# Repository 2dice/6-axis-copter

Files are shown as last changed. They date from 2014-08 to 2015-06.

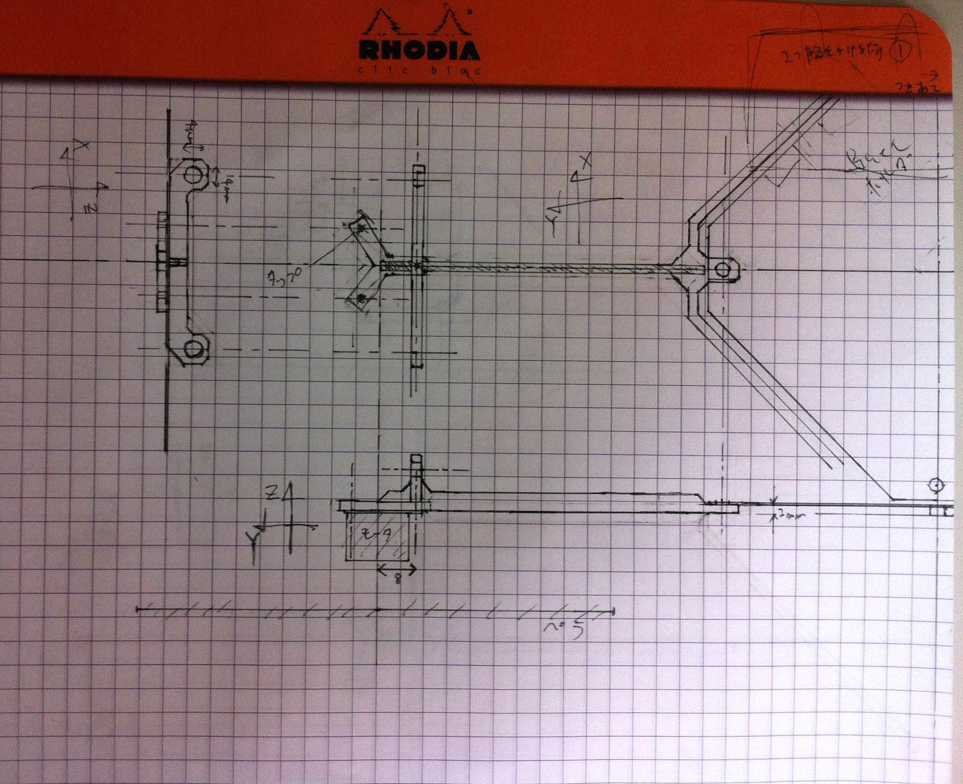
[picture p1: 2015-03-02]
devlog/picture/2015.03.01_2xframe_draft-1.JPG

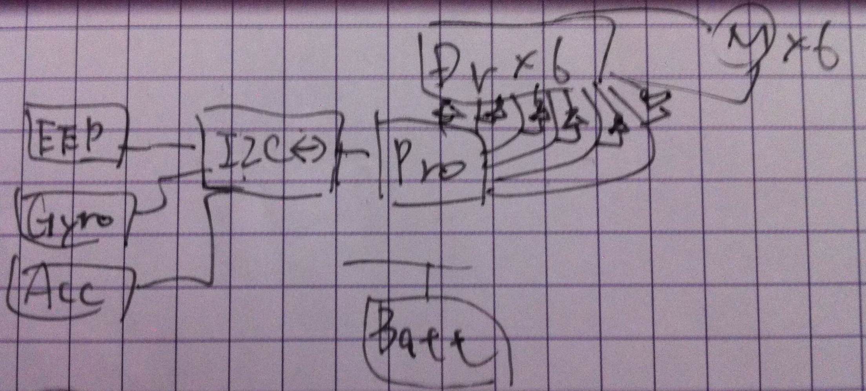
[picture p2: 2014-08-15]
devlog/picture/2014.08.09_circuit-block-image.JPG

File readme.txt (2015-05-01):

■6軸コプター概要
6軸に移動可能なマルチコプターを6個のプロペラで実現することを目標としている．
最終的には自動で衝突回避・PCからコマンドを受信しアクロバットな動きをさせる．

■開発フェーズ
ラフ設計段階
・電子回路
	1x基板(コアレス->ブラシモータ)浮力不足により2xでブラシレスモータ試作
	2x基板作成中
・アクチュエータ
	ブラシレスモータ・プロペラ仮選定済み．2xで浮力確認
・ソフトウェア
	デバイスドライバ仮実装完了．
	2x基板作成後最終確認．その後モータ制御実装．
・筐体
	2x向け設計完了(3Dプリント中)

■ディレクトリ構成
./datasheet
	電子回路に使用している部品のデータシート置き場
./devlog
	開発記録
./schematic
	**.sch
		回路図(kicad)
	**.kicad_pcb
		基板図(kicad)
	librarys
		回路図に使用したライブラリ(kicad)
	gbr
		P板.com提出ファイル(板厚0.6mmで発注)
	**.pdf
		回路図
	**.FCStd
		筐体3D-CAD設計ファイル(FreeCAD)
	**.stl
		DMM.make提出ファイル(3Dプリンタ用STLファイル)
./src
	ソフトウェア
	環境構築は以下を参照
	http://qiita.com/2dice/items/70c5abf6259508660bce
./src/tools/6-axis-monitor
	無線通信(zigbee)によるモニタツール(Qt)
	zigbee環境構築方法は作成中

■構成
・プロペラ配置は3d図面及び./devlog/pictureを参照
・ブラシレスモータとリポバッテリ(3セル直列)を使用
・移動量は3軸ジャイロ及び3軸加速度センサでモニタ
・EEPROMにチューニングパラメータを保存
・測距センサを全軸に付け，衝突を回避するようなロジックを入れる
・デバイスの電源電圧の都合上4.5V/3.6Vの2電源を生成．
  本来I/Fにレベルシフタを入れるべきだが抵抗で保護し実力で故障回避を狙う．
  そのため電源電圧を極力近づける設計とした．

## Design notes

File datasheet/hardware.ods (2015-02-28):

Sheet: 基本情報
マイコン
 | ROM | 512kバイト
 | 内蔵RAM | 16kバイト
 | 外付けRAM | 16Mbit | 最大64Mbit対応可能
 | 16bitタイマー | 3ch
 | 8bitタイマー | 4ch
 | プログラマブルタイミングパターンコントローラ | あり
 | WDT | あり
 | SCI | 3ch
 | 10bitADコンバータ | 8ch
 | 8bitDAコンバータ | 2ch
 | DMAコントローラ | 4ch
 | I/Oポート | 79ch(max)
 | バスコントローラ | あり
 | 発振子周波数(システムクロック) | 25MHz
 | ボードURL | http://akizukidenshi.com/catalog/g/gK-05578/

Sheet: デバイス情報
マイコン
 | ROM | 512kバイト
 | 内蔵RAM | 16kバイト
 | 外付けRAM | 16Mbit | 最大64Mbit対応可能
 | 16bitタイマー | 3ch
 | 8bitタイマー | 4ch
 | プログラマブルタイミングパターンコントローラ | あり
 | WDT | あり
 | SCI | 3ch
 | 10bitADコンバータ | 8ch
 | 8bitDAコンバータ | 2ch
 | DMAコントローラ | 4ch
 | I/Oポート | 79ch(max)
 | バスコントローラ | あり
 | 発振子周波数(システムクロック) | 25MHz
 | ボードURL | http://akizukidenshi.com/catalog/g/gK-05578/
I2Cバスコントローラ
 | PCA9665PW
 | ※CS1でアドレスデコードされ，200000H~200003Hで使用可能
 | サイズ= | 24 | bit
EEPROM
 | R1EX24512BTA
 | I2CデバイスID：0xA0,0xA1
加速度センサ
IC16 | ADXRL345
 | I2CデバイスID：0x53
角速度センサ
IC17 | AE-L3GD20
 | I2CデバイスID：0xD5,0xD4
シリアルドライバ
IC22 | ADM3202
DRAM
IC20 | MSM5117805F-60TK
 | ※sc2でアドレスデコードされ，400000H~5FFFFFH(エリア2)で使用可能
 | サイズ= | 16777208 | bit | 2097151 | byte
 | ※EDO(エクステンドデータアウト)DRAMなのでバーストモードは使用不可
 | DRAMコントロールレジスタA(DRCRA)のビット3バーストアクセスイネーブル(EB)は0(バースト禁止)に設定すること
 | リフレッシュ周期2048cyc/32ms以内
測距センサ
IC8~12 | GP2Y0A21YK
 | AD入力に接続
モータドライバ
IC1~6 | TB6588FG
 | AD入力によるBLDCドライバ

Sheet: ポート表
 | MD0 | MD1 | MD2 | FWE | NMI
SW1設定 | 1 | 2 | 3 | 4 | 5
FLASH書き込み | 1 | 1 | 0 | 1 | 1
動作mode5 | 1 | 0 | 1 | 0 | 1
H8/3069F | mode5
pin_No | 接続先 |  |  | 設定 | 機能
1 |  | 0.1u |  | - | VCL(内部降圧端子)
2 | CN1-33pin | MOTER_PWM_4 |  |  | /CS7 | TMO0 | TP8 | PB0
3 | CN1-34pin | MOTER_PWM_5 |  |  | /CS6 | /DREQ0 | TMIO1 | TP9 | PB1
4 | CN1-35pin | MOTER_PWM_6 |  |  | /CS5 | TMO2 | TP10 | PB2
5 | CN1-36pin | MOTOR_DIR_6 |  | 出力L | /CS4 | /DREQ1 | TMIO3 | TP11 | PB3
6 | CN1-37pin | IC20-23pin(/CAS) |  |  | /UCAS | TP12 | PB4
7 | CN1-38pin |  |  | 出力L | SCK2 | /LCAS | TP13 | PB5
8 | CN1-39pin | ZigBeeRx |  |  | TxD2 | TP14 | PB6
9 | CN1-40pin | ZigBeeTx |  |  | RxD2 | TP15 | PB7
10 |  | SW1-4pin(pull-down) |  |  | FWE
11 |  | GND |  |  | VSS
12 |  | IC5-11pin(Tx1in) |  | 出力L | TxD0 | P90
13 |  | IC5-10pin(Tx2in) |  |  | TxD1 | P91
14 |  | IC5-12pin(Rx1out) |  | 入力 | RxD0 | P92
15 |  | IC5-9pin(Rx2out) |  |  | RxD1 | P93
16 | CN2-3pin |  |  | 出力L | /IRQ4 | SCK0 | P94
17 | CN2-4pin |  | /IC19-16pin(INT) |  | /IRQ5 | SCK1 | P95
18 | CN2-5pin |  |  | 出力L | D0 | P40 |  |  |  | ※P4は内部プルアップ可能
19 | CN2-6pin |  |  | 出力L | D1 | P41 |  |  |  | ※P4n選択不可
20 | CN2-7pin |  |  | 出力L | D2 | P42
21 | CN2-8pin |  |  | 出力L | D3 | P43
22 |  | GND |  |  | VSS
23 | CN2-9pin |  |  | 出力L | D4 | P44
24 | CN2-10pin |  |  | 出力L | D5 | P45
25 | CN2-11pin |  |  | 出力L | D6 | P46
26 | CN2-12pin |  |  | 出力L | P47 | D7
27 | CN2-13pin | IC20-2pin(D0) | IC19-1pin(D0) |  | P30 | D8 |  |  |  | ※P3n選択不可
28 | CN2-14pin | IC20-3pin(D1) | IC19-2pin(D1) |  | P31 | D9
29 | CN2-15pin | IC20-4pin(D2) | IC19-3pin(D2) |  | P32 | D10
30 | CN2-16pin | IC20-5pin(D3) | IC19-4pin(D3) |  | P33 | D11
31 | CN2-17pin | IC20-24pin(D4) | IC19-5pin(D4) |  | P34 | D12
32 | CN2-18pin | IC20-25pin(D5) | IC19-6pin(D5) |  | P35 | D13
33 | CN2-19pin | IC20-26pin(D6) | IC19-7pin(D6) |  | P36 | D14
34 | CN2-20pin | IC20-27pin(D7) | IC19-8pin(D7) |  | P37 | D15
35 |  | 5V |  | - | VCC
36 | CN2-21pin | IC20-10pin(A0) | IC19-14pin(A0) |  | P10 | A0 |  |  |  | ※P1nは入力専用(出力不可)
37 | CN2-22pin | IC20-11pin(A1) | IC19-15pin(A1) |  | P11 | A1
38 | CN2-23pin | IC20-12pin(A2) |  |  | P12 | A2
39 | CN2-24pin | IC20-13pin(A3) |  |  | P13 | A3
40 | CN2-25pin | IC20-16pin(A4) |  |  | P14 | A4
41 | CN2-26pin | IC20-17pin(A5) |  |  | P15 | A5
42 | CN2-27pin | IC20-18pin(A6) |  |  | P16 | A6
43 | CN2-28pin | IC20-19pin(A7) |  |  | P17 | A7
44 |  | GND |  |  | VSS
45 | CN2-29pin | IC20-20pin(A8) |  |  | P20 | A8 |  |  |  | ※P2nは内部プルアップ可能
46 | CN2-30pin | IC20-21pin(A9) |  |  | P21 | A9 |  |  |  | ※P2nは入力専用(出力不可)
47 | CN2-31pin | IC20-9pin(A10) |  |  | P22 | A10
48 | CN2-32pin |  |  | 入力 | P23 | A11
49 | CN2-33pin |  |  | 入力 | P24 | A12
50 | CN2-34pin |  |  | 入力 | P25 | A13
51 | CN2-35pin |  |  | 入力 | P26 | A14
52 | CN2-36pin |  |  | 入力 | P27 | A15
53 | CN2-37pin |  |  | 入力 | P50 | A16 |  |  |  | ※P5nは内部プルアップ可能
54 | CN2-38pin |  |  | 入力 | P51 | A17 |  |  |  | ※P5nは入力専用(出力不可)
55 | CN2-39pin |  |  | 入力 | P52 | A18
56 | CN2-40pin |  |  | 入力 | P53 | A19
57 |  | GND |  | - | VSS
58 | CN1-1pin |  |  | 出力L | P60 | /WAIT
59 | CN1-2pin |  |  | 出力L | P61 | /BREQ
60 | CN1-3pin |  |  | 出力L | P62 | /BACK
61 | CN1-4pin |  |  |  | P67 | φ(CLK) |  |  |  | ※P67は入力専用(出力不可)
62 |  | 4.5V |  | - | /STBY
63 |  | Pull-up |  | - | /RES
64 | CN1-5pin | Pull-up |  | - | NMI
65 |  | GND |  | - | VSS
66 |  | X2(25MHz) |  | - | EXTAL
67 |  | X2(25MHz) |  | - | XTAL
68 |  | 5V |  | - | VCC
69 | CN1-6pin |  |  |  | P63 | /AS |  |  |  | ※P63~P66は選択不可
70 | CN1-7pin | IC20-6pin(/WE) | IC19-11pin(/WR) |  | P64 | /RD
71 | CN1-8pin |  | IC19-12pin(/RD) |  | P65 | /HWR
72 | CN1-9pin |  |  |  | P66 | /LWR
73 |  | SW1-1pin(pull-down) |  |  | MD0
74 |  | SW1-2pin(pull-down) |  |  | MD1
75 |  | SW1-3pin(pull-down) |  |  | MD2
76 | CN1-10pin | 4.5V |  |  | AVCC
77 | CN1-11pin | 4.5V |  |  | VREF
78 | CN1-12pin | DISTANCE_1 |  | 入力 | AN0 | P70 |  |  |  | ※P7nは入力専用(出力不可)
79 | CN1-13pin | DISTANCE_2 |  | 入力 | AN1 | P71
80 | CN1-14pin | DISTANCE_3 |  | 入力 | AN2 | P72
81 | CN1-15pin | DISTANCE_4 |  | 入力 | AN3 | P73
82 | CN1-16pin | DISTANCE_5 |  | 入力 | AN4 | P74
83 | CN1-17pin | DISTANCE_6 |  | 入力 | AN5 | P75
84 | CN1-18pin | Bat_V |  | 入力 | DA0 | AN6 | P76
85 | CN1-19pin | Bat_I |  | 入力 | DA1 | AN7 | P77
86 |  | GND |  | - | AVSS
87 | CN1-20pin |  |  | 出力L | /RFSH | /IRQ0 | P80 |  |  | ※P80~82はシュミット入力
88 | CN1-21pin |  |  |  | /CS3 | /IRQ1 | P81 |  |  | ※P81~P84は入力専用(出力不可)
89 | CN1-22pin | IC20-7pin(/RAS) | Pull-up |  | /CS2 | /IRQ2 | P82 |  |  | DRAMで複数エリア共通CSによりCS3を使ってなければP81は出力可能
90 | CN1-23pin |  | IC19-13pin(CE) |  | /ADTRG | /CS1 | IRQ3 | P83
91 | CN1-24pin |  |  | 入力 | /CS0 | P84
92 |  | GND |  | - | VSS
93 | CN1-25pin | MOTOR_DIR_1 |  |  | /TEND0 | TCLKA | TP0 | PA0 |  | ※PＡnはシュミット入力
94 | CN1-26pin | MOTOR_DIR_2 |  |  | /TEND1 | TCLKB | TP1 | PA1
95 | CN1-27pin | MOTER_PWM_1 |  |  | TCLKC | TIOCA0 | TP2 | PA2
96 | CN1-28pin | MOTOR_DIR_3 |  |  | TCLKD | TIOCB0 | TP3 | PA3
97 | CN1-29pin | MOTER_PWM_2 |  |  | A23 | TIOCA1 | TP4 | PA4
98 | CN1-30pin | MOTOR_DIR_4 |  |  | A22 | TIOCB1 | TP5 | PA5
99 | CN1-31pin | MOTER_PWM_3 |  |  | A21 | TIOCA2 | TP6 | PA6
100 | CN1-32pin | MOTOR_DIR_5 |  |  | A20 | TIOCB2 | TP7 | PA7
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

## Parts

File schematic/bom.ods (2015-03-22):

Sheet: bom
購入：x, 調達：y |  |  |  |  |  |  | ※2015.02.28時の価格.コストよりも極力少ない店舗数で購入することを優先し選定
 | Qty | Value | Device | Parts No. | 購入ショップ | URL | cost[¥]
- | 1 | H8-PRO-BOARD | AKI-H8/3069Ｆマイコンボードキット完成品DRAM付き | BD200 | 秋月 | http://akizukidenshi.com/catalog/g/gK-02298/ | 2700 | Pro用なら¥2,000(セルフ実装)
- |  | 分割ロングピンソケ |  | ↑ | 秋月 | http://akizukidenshi.com/catalog/g/gC-05779/ | 99.6904761905
- | 8 | 100p | C1608C0G2A101F | C112,C122,C604,C614,C624,C634,C644,C654 | chip1stop | http://www.chip1stop.com/dispDetail.do?partId=TDK1-0045752&mpn=C1608C0G2A101F | 2368
- | 2 | 0.01u | GRM188B11H103KA01 | C111,C121 | 秋月 | http://akizukidenshi.com/catalog/g/gP-04660/ | 2
- | 19 | 0.1u | GRM188F11H104ZA01 | C130,C140,C300,C400,C410,C420,C430,C440,C450,C500,C510,C520,C530,C608,C618,C628,C638,C648,C658 | 秋月 | http://akizukidenshi.com/catalog/g/gP-04940/ | 9.5
- | 12 | 0.47u | C1608X5R1C474K | C602,C607,C612,C617,C622,C627,C632,C637,C642,C647,C652,C657 | chip1stop | http://www.chip1stop.com/dispDetail.do?partId=TDK1-0049530&mpn=C1608X5R1C474K | 16.68
y10 | 16 | 1u | GRM188F11C105ZA01 | C110,C113,C120,C123,C600,C603,C610,C613,C620,C623,C630,C633,C640,C643,C650,C653 | 秋月 | http://akizukidenshi.com/catalog/g/gP-02996/ | 32
- | 6 | 10u(3216) | GRM31CF11E106Z | C601,C611,C621,C631,C641,C651 | 秋月 | http://akizukidenshi.com/catalog/g/gP-01185/ | 75
- | 1 | 22u(3225) | GRM31CB31E226KE15 | C100 | 秋月 | http://akizukidenshi.com/catalog/g/gP-06038/ | 20
- | 1 | S3B-XH-A | S3B-XH-A | CN100 | chip1stop | https://www.chip1stop.com/dispDetail.do?partId=JST1-0004585&mpn=S3B-XH-A%28LF%29%28SN%29 | 33
- | 1 | LIPO-BATT | KYPOM K6 7.4V 450mA 35C-70C //59A5A | ↑ | KK HOBBY | http://www.kkhobby.com/SHOP/BT171.html | 535 | 充電器→ | http://www.kkhobby.com/SHOP/HM44165.html
- | 7 | SR54F | SR54F | D100,D600,D610,D620,D630,D640,D650 | 秋月 | http://akizukidenshi.com/catalog/g/gI-06125/ | 1750
- | 1 | MF-SM300-2 | MF-SM300-2 | F1 | chip1stop | http://www.chip1stop.com/dispDetail.do?partId=BOUR-0011938&mpn=MF-SM300-2 | 65.2
x5 | 2 | NJM111000F1 | NJM11100F1 | IC110,IC120 | 秋月 | http://akizukidenshi.com/catalog/g/gI-06655/ | 60
x3 | 1 | LT6106CS5 | LT6106CS5 | IC21 | 秋月 | http://akizukidenshi.com/catalog/g/gI-07300/ | 210
- | 1 | TWE-LITE | TWE-LITE-DIP-WA | IC300 | 秋月 | http://akizukidenshi.com/catalog/g/gM-06760/ | 1945
- | 1 |  | TWE-Lite-R-IC | ↑ | 秋月 | http://akizukidenshi.com/catalog/g/gM-08264/ | 2430 | TWE-LITEソフト書き込みツール
- | 1 |  | TWE-Lite-USB-C | ↑ | 秋月 | http://akizukidenshi.com/catalog/g/gM-07232/ | 2980 | PC用TWE-LITE受信モジュール
- | 6 | GP2Y0A21YK | GP2Y0A21YK | IC400,IC410,IC420,IC430,IC440,IC450 | 秋月 | http://akizukidenshi.com/catalog/g/gI-02551/ | 2700
- | 12 | M2.5ネジ・ナット |  | ↑
x3 | 1 | PCA9665PW | PCA9665PW | IC500 | chip1stop | https://www.chip1stop.com/dispDetail.do?partId=NXP1-0038353&mpn=PCA9665PW,112 | 82
- | 1 | ADXL345 | ADXL345 | IC510 | 秋月 | http://akizukidenshi.com/catalog/g/gM-06724/ | 450
x2 | 1 | R1EX24512BTA | R1EX24512BTA | IC530 | マルツ | http://www.marutsu.co.jp/GoodsDetail.jsp?salesGoodsCode=238624&shopNo=3 | 421
- | 6 | TB6588FG | TB6588FG,8,EL,JU | IC600,IC610,IC620,IC630,IC640,IC650 | chip1stop | https://www.chip1stop.com/dispDetail.do?partId=TOSH-0103957 | 8040 | 在庫なし，取り寄せ依頼
x8 | 6 | HK-AP05 3000KV | HK-AP05 3000KV | M600,M610,M620,M630,M640,M650 | ホビーショップα or ホビーキング | http://www.hs-alfa.com/menew/motor/burasires/ds-HK-AP05%203000kv.htm | 17940 | http://agent.selfis.tv/hobbyking-guide
x8 | 6 | GWS4025 | GWS4025 | ↑ | ホビーショップα or ホビーキング | http://www.hs-alfa.com/menew/puropera/gws%20dd_sf.html | 1602 | http://agent.selfis.tv/hobbyking-guide
x20 | 18 | M1.2モータ固定ネジ |  | ↑ |  | http://www.amazon.co.jp/HPIジャパン-103623-サラタッピングネジ-M1-2×4mm-10pcs/dp/B004Q0WRHO | 990.2
x2 | 1 | 0.02D(3216) | CRL1206-FU-R020ELF | R7 | chip1stop | https://www.chip1stop.com/dispDetail.do?partId=BOUR-0062498&mpn=CRL1206-FU-R020ELF | 345
x10 | 6 | 0.2F(2012) | SR732ATTDR200F | R606,R616,R626,R636,R646,R656 | chip1stop | https://www.chip1stop.com/dispDetail.do?partId=KOA1-1127358&mpn=SR732ATTDR200F | 345.6
- | 6 | 1kJ | RK73B1JTTD102J | R603,R613,R623,R633,R643,R653 | chip1stop | http://www.chip1stop.com/dispDetail.do?partId=KOA1-1085217&mpn=RK73B1JTTD102J | 60.6
y10 | 9 | 1.5kJ | RK73B1JTTD152J | R111,R143,R400,R410,R420,R430,R440,R450,R500 | chip1stop | http://www.chip1stop.com/dispDetail.do?partId=KOA1-1086185&mpn=RK73B1JTTD152J | 90.9
- | 1 | 3.3kJ | RK73B1JTTD332J | R121 | chip1stop | http://www.chip1stop.com/dispDetail.do?partId=KOA1-1085241&mpn=RK73B1JTTD332J | 10.1
- | 1 | 3.9kJ | RK73B1JTTD392J | R110 | chip1stop | http://www.chip1stop.com/dispDetail.do?partId=KOA1-1086682&mpn=RK73B1JTTD392J | 10
- | 9 | 4.7kJ | RK73B1JTTD472J | R200,R501,R502,R600,R610,R620,R630,R640,R650 | chip1stop | http://www.chip1stop.com/dispDetail.do?partId=KOA1-1085248&mpn=RK73B1JTTD472J | 30.87
- | 1 | 6.2kJ | RK73B1JTTD622J | R120 | chip1stop | http://www.chip1stop.com/dispDetail.do?partId=KOA1-1121904&mpn=RK73B1JTTD622J | 66.6
- | 15 | 10kJ | RK73B1JTTD103J | R130,R131,R142,R604,R605,R614,R615,R624,R625,R634,R635,R644,R645,R654,R655 | chip1stop | http://www.chip1stop.com/dispDetail.do?partId=KOA1-1085220&mpn=RK73B1JTTD103J | 151.5
- | 6 | 20kJ | RK73B1JTTD203J | R602,R612,R622,R632,R642,R652 | chip1stop | http://www.chip1stop.com/dispDetail.do?partId=KOA1-1087589&mpn=RK73B1JTTD203J | 360
- | 6 | 220kJ | RK73B1JTTD224J | R601,R611,R621,R631,R641,R651 | chip1stop | http://www.chip1stop.com/dispDetail.do?partId=KOA1-1086680&mpn=RK73B1JTTD224J | 360
- | 1 | 200J | RK73B1JTTD201J | R141 | chip1stop | http://www.chip1stop.com/dispDetail.do?partId=KOA1-1085811&mpn=RK73B1JTTD201J | 10
- | 3 | 1kJx4 | BCN164AB102J7LF*10 | RA500,RA501,RA502 | マルツ | http://www.marutsu.co.jp/pc/i/14217/ | 30
x10 | 6 | 10kJx4 | BCN164AB103J7LF | RA600,RA610,RA620,RA630,RA640,RA650 | マルツ | http://www.marutsu.co.jp/GoodsDetail.jsp?salesGoodsCode=14220&shopNo=3 | 60
- | 1 | SS12D01G4 | SS12D01G4 | SW100 | 秋月 | http://akizukidenshi.com/catalog/g/gP-02736/ | 25
- | 1 | PCB | 6軸コプター2x基板 |  | P板.com |  | 17836 | ２枚製造(FR4標準2層_板厚0.6mm両面シルク)
- | 4 | M2.5ネジ・ナット |  | ↑
x1 | 1 | 筐体 | 6軸コプター2x用筐体 |  | DMM.make |  | 3692
計 | 216 |  |  |  |  |  | 71040

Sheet: 購入
 | Qty | Value | Device | Parts No. | 購入ショップ | URL | cost[¥]
x5 | 2 | NJM111000F1 | NJM11100F1 | IC110,IC120 | 秋月 | http://akizukidenshi.com/catalog/g/gI-06655/ | 60
x3 | 1 | LT6106CS5 | LT6106CS5 | IC21 | 秋月 | http://akizukidenshi.com/catalog/g/gI-07300/ | 210
x3 | 1 | PCA9665PW | PCA9665PW | IC500 | chip1stop | https://www.chip1stop.com/dispDetail.do?partId=NXP1-0038353&mpn=PCA9665PW,112 | 82
x2 | 1 | R1EX24512BTA | R1EX24512BTA | IC530 | マルツ | http://www.marutsu.co.jp/GoodsDetail.jsp?salesGoodsCode=238624&shopNo=3 | 421 |  | 製品ID | 製品名 | 在庫 | 出荷先
x8 | 6 | HK-AP05 3000KV | HK-AP05 3000KV | M600,M610,M620,M630,M640,M650 | ホビーショップα or ホビーキング | http://www.hs-alfa.com/menew/motor/burasires/ds-HK-AP05%203000kv.htm | 17940 | http://agent.selfis.tv/hobbyking-guide | HK-AP05-3000 | HobbyKing AP05 3000kv Brushless Micro Motor (5.4g) | 10
x6 | 6 | GWS4025 | GWS4025 | ↑ | ホビーショップα or ホビーキング | http://www.hs-alfa.com/menew/puropera/gws%20dd_sf.html | 1602 | http://agent.selfis.tv/hobbyking-guide | 25000115 | GWS EP Propeller (DD-4025 102x64mm) grey (6pcs/set) | 10
x20 | 18 | M1.2モータ固定ネジ |  | ↑ |  | http://www.amazon.co.jp/HPIジャパン-103623-サラタッピングネジ-M1-2×4mm-10pcs/dp/B004Q0WRHO | 990.2
(x2) | 1 | 0.02D(3216) | CRL1206-FU-R020ELF | R7 | chip1stop | https://www.chip1stop.com/dispDetail.do?partId=BOUR-0062498&mpn=CRL1206-FU-R020ELF | 345
x10 | 6 | 0.2F(2012) | SR732ATTDR200F | R606,R616,R626,R636,R646,R656 | chip1stop | https://www.chip1stop.com/dispDetail.do?partId=KOA1-1127358&mpn=SR732ATTDR200F | 345.6
x10 | 6 | 10kJx4 | BCN164AB103J7LF | RA600,RA610,RA620,RA630,RA640,RA650 | マルツ | http://www.marutsu.co.jp/GoodsDetail.jsp?salesGoodsCode=14220&shopNo=3 | 60

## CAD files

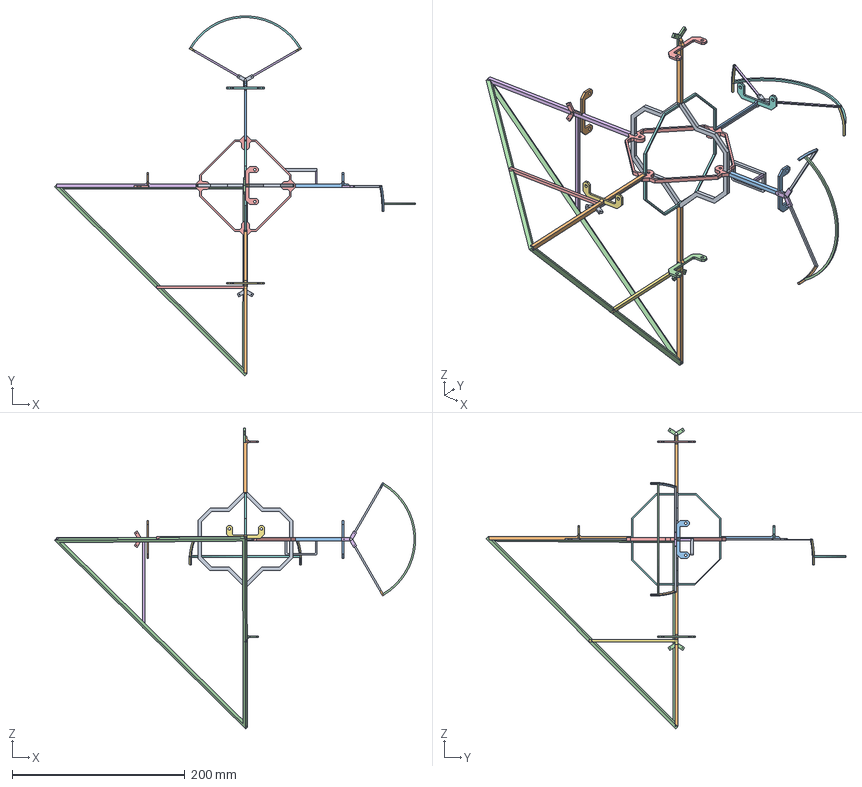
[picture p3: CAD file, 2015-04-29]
schematic/frame_for_2x.FCStd
418.1 x 416.8 x 348.4 mm
Z_pcb-holder001
Z_bar002
Y_bar-aid+001
Z_motor-holder001
X_motor-holder-001
X_motor-holder+001
Y_distance-holder-001
Y_distance-holder+001
Batt-holder001
X_distance-holder-001
X_distance-holder+001
Z_distance-holder-001
Z_distance-holder+001
Y_propeller_gard1+001
Y_propeller_gard2+001
Y_propeller_gard4+001
X_propeller_gard2+001
X_propeller_gard3+001
X_propeller_gard4+001
X_propeller_gard5+001
XY_pcb-holder001
Batt-holder-aid001
Y_propeller_gard3+001
Y_rot_aid001
Y_motor-holder001
Y_bar-aid-001
X_bar001
base001
base-aid007
base-aid008
base-aid010

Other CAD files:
schematic/frame_for_2x.stl

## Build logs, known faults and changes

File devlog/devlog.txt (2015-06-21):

////////////////////
2015.06.21
モニタツールにボタンを追加してシリアルでコマンド送信できるようにしよう．
とりあえず画面がグラフでいっぱいだから寄せよう．
qmlでボタン追加．ボタンがそっけないけど今のところいいか．
onClicked()でctrlオブジェクトの関数を呼ぶ．
コマンドごとに関数分けるの面倒だから引数でコマンド取らせよう．
ctrlからserial_ifの関数を呼び出せるようにしたら普通に送れた．
そのうちクリックした瞬間だけボタンの色を変えるようにしよう．

////////////////////
2015.06.20
制御実装状態で何が起きているか分かるようにしたい．
モニタツールでグラフを作っては見たものの，
物とモニタを同時に見れないからデータが流れる．
データが来て無くても自動で流れちゃうのは何とかしたい．
データが無ければ描画のタイマを止めるような処理を組み込みたい．
->エレメントの更新がなければd1の値が-1になるようにし，
  qmlタイマでd1=-1だったら値更新しないように変更．うまくいった．
簡易的に全てのデータを俯瞰できるようにツールを改造する．
案1
  各値をタブ区切りでdebugコンソールに出してlibreで見る
案2
  当初の予定通り，データの保存・再生動作を組み込む
簡易的には案1がいいか．
→タブにしなくてもvimに貼り付けてからlibreに貼るとうまくいった
-
制御処理はif文で4回に分けてるから，3回分のセンサデータは捨ててる．
ave=(ave+今回値)/2で簡易的に前回値と今回値の移動平均しよう．
→角加速度の初期値がずれてるからZ軸だけ回っちゃう．
  加速度の初期値をわけて再挑戦．各センサ値の出力を制御に使う値に変更した．
  回らなくなったけど浮かないからペラ変更．
  →GWS4040にしたけど浮かない．
-
一時的な脱調対策
Battラインにコンデンサ追加．
まずは全ドライバICの電源10uに22uセラコンを入れてみる．
->改善しない
  更に電解コン100uF追加
  ->だめだ．これが原因じゃない．やっぱフレームがぶれて振動で脱調してる？
-
センサのゼロ点を補正する
一旦pwmセッターをコメントアウトしてペラが回らないようにし，
角速度/加速度の平均値を出力
->GXは平均-20
  GY:7.6
  GZ:-20
  AX:142
  AY:146
  AZ:168
  これを元にゼロ点を指定．Gyro値は概ね0に近いから移動平均で回ってるか見よう

////////////////////
2015.06.13
C646:0.01u実装完了
ポリスイッチショート=>85->88でLowbatt．
あんま変わらないBatt電圧11.4Vだから充電して再挑戦
->12.3Vだと97まで脱腸しなくなった．浮きそう．
  でもZ軸を中心に回るからGyro積分必要そう．
ようやく制御プログラム作成に移れる．
だたし，たまに一瞬脱調して復帰するような挙動が起こるのだけは何とかしたい．
浮力ががくっと落ちるから制御が狂う．

////////////////////
2015.05.30
ドライバIC届いた．付け替えだるい．
1pinずつ剥がすの難しい．ランド剥がれた．
ランド周囲にレジストかぶせれば強度上がるからそうすればよかった．
motorDirのランドが消えたからpin浮かせてUEWで無理やり接続．
なんとかペラ回った．復旧完了
あとはC646を0.01uに変更する．在庫ないから調達しようと思って忘れてた．
-
450mAhのリポ到着．偶然にもバッテリホルダにピッタリはまった．
350mAhのリポでちょっと余裕あるように設計したつもりだったけど
測ったようにピッタリ．運が良かった．
-
PWMがALL86でLowBattに入る．
電圧が落ちてるからなのかポリスイッチがトリップしてるのか．．．
充電して再確認しよう．
-
そういや写真撮る前に筐体加工しちゃったな．後で撮ろう．

////////////////////
2015.05.24
C646をOPEN->0.01uFに変更(時定数0.1ms,カットオフ1.59kHz)．
  84%でLowBatt．4Vまで上がったからほぼmax．ビンゴっぽい．
  結構早めにLowBattになるからリポを350mAh->450mAhに変更しよう
壊れてるモータードライバ問題．
過負荷で壊れたんなら他のも危ない．正常なIC触ってみると結構熱い．
電源電圧が高いからモーター電流が大きい？モーターに直列に抵抗入れてみる．
昨日確認した単独確認セット(0x改造品)で確認
  0.3Ωx3でも５秒ぐらいで触れなくなる．
  1Ωx3だとちょうど良さそうな感じ．適用しよう．
  2Sにすると負荷でICの下限電圧7Vを切るけど，3Sだと高い．
  3Sで抵抗に電力食わせるとちょうどいいっぽい．これで電力的に壊れることはない．
抵抗入れたら91%までいった．LowBattになる問題はあるから450mAh品に変えよう
修理用にドライバIC追加購入する．リペアめんどくせぇなぁ
ただ一時的に回転数が落ちて復帰するような挙動をすることはある．
進み角を30度つけてみる．
  こっちのほうが多少脱調しにくい．結局最初の設定だ．でもまだ脱調する．

////////////////////
2015.05.23
レギュレータ変更完了．落ちなくなった．
電圧が4.782V．あわない．計算は正しそう．微調整面倒だからこれでいいか．
バッテリ低下の判定電圧だけ合わせよう．
ドライバのVSPは1.2V~4.1VだからPWMの理論値は25%~90%．90%までに飛ぶか確認
  75%で脱調しちゃうペラがある
試しに進み角を0度->30度(LA1=LA2=H)に
  変わらない
外れるYnだけ，進み角0度ラップ無し(LA1=LA2=L,SEL_LAP=H)
  関係ないけどZpペラが回らなくなった．熱いから電流はいってる？
  モーターの抵抗値がちょい高いから部分OPENかも
    モーター交換したけど動かない．波形見るとドライバにDCがかかってる．
    ドライバ壊れた．．．
  モータOPENでとりあえずラップ無し効果確認．
  ->80でLowBattになったけど脱調してない．効果ありそう？
    チャージして再確認したら75%で脱調する．変わらねぇじゃねぇか．
->このドライバで脱調せずに安定制御はできない．方式を再検討しよう．
センサレスでなければ脱調は緩和されるはず．ホール素子付きモーター探そう．
探してみるとマルチコプター用モーター・ESCはセンサレスしか無いっぽい．
センサー度は重いしデカいから不向き？低回転高トルクのほうが特異なのかも．
市販のESCだとちゃんと回せてるんだから，制御がちゃんとしてれば回せるはず．
市販のESCは中に小型マイコンとFETが入ってるっぽい．
一回探してるだけあって意外と見つからない．
今のドライバに外付けFETでブーストしたら電流増えるかな？
波形を見る限りPWMは電源電圧まで触れてるからFET能力不足ではなさそう．
単独で脱調するかどうか確認しよう．もしかして過電流制限かかって止まってる？
  単独だと脱調してない．過電流検知はフル回転で0.35Vだから1.75Aまでしか行かない
  まぁ定格は超えるけど．．．
  カレントリミットだとしたらフィルタをキツ目にかけてみよう．
  C646をOPEN->0.01uFに変更(時定数1ms,カットオフ159Hz)．
  だめならWAVEMがノイズで誤検知してタイミングずれてるかも．C645に1000p

////////////////////
2015.05.17
測距センサ外したら4.5V落ちなくなった．レギュレータ変えればいけそう．
届いたらやってみよう．

////////////////////
2015.05.16
・脱調するならデカップリングコン追加
  ->22ux2追加．変わらない
・ペラ径落として99%まで脱調しないようにする
  ->5030:86で脱調，昨日は93%だったはず．温度？バッテリ電圧？
  ->4040:89で脱調
  ->4025:90でlowbatt
  再確認
  ->4025:99で脱調せず
  ->4040:99で脱調したりしなかったり(飛ばない)
  ->5030:94~98で脱調，飛ばない
  試しにYp/Ynだけで5030で試す(斜めにしない本来やろうと思ってた姿勢)
    ->100gぐらいしか浮力でない．全然浮かない(重量210g)
  バッテリ電圧が低いと脱調しやすくなる！
・VSPをmaxまで出せてるか確認
  99%2.8Vくらい．4V目標なのに全然出てない．ドライバIC内部抵抗1kくらい．ひどい
  100Ωくらいにしないと無理
  100Ωにしても2.9V．そもそもマイコン出力側が出てない？
  10kだとちゃんと0V-4.6V出るけど100Ωだと0.5V-3Vくらい．
  マイコン出力電流が間に合ってない．
  4.7kだと0.1V-4.4V．そこそこいいとこ．
  なのに4.7kだと2.6Vまでしか上がらない．
  4.5Vが結構ゆれてる？->揺れて2.5Vくらいまで落ちるところもある．
  1ms周期で落ちるからレギュレータの負荷応答？4.5Vに2.2uF足しても変わらず．
  DRAMを初期化せずに変更してもかわらない．レギュレータ変えなきゃダメか．
  データシートでは測距センサ30mA*6+マイコン24mA,DRAM120mA=324mA.
  レギュレータは320mA出せるからそんなに実力で落ちるとは思えないが．．．
  3.6Vは落ちてない．
  4.5V側はAZ1117H-ADJ買って試してみよう．7mm角で1.3A出せる
  C113:22uF,R111:3.9k,R110:1.5k,R112:OPEN
  秋月で購入予定．
  それまで試しに測距センサx6をOPENにして試してみよう．-180mAにはなるはず

////////////////////
2015.05.13
ラップ書けたらGWS5030でも99%まで脱調しなくなった．いける．
全部にラップかけると93%で脱調した．
この段階で三角形の足を切断し，糸で突っ張ったがまだ飛ばない．
そもそもモーター変えて飛ぶのか？
とりあえず苦し紛れにバッテリのデカップリングコン増やしてみよう．
ペラ径落として99%まで回したほうが浮力出るかも
99%5030で飛ばなかったらVSP電圧値確認->ペラ大型化(5043,6030,6050,7035)
99%で飛ばないならモーター変えても一緒．ペラ径で稼ぐしか無い．
これからやることまとめ
・ペラ径落として99%まで脱腸しないようにする
・脱調するならデカップリングコン追加
・脱調しなくなればVSPをmaxまで出せてるか確認
・脱調しなくなればペラ大型化

////////////////////
2015.05.12
ペラ到着．4040でさえ87%で脱調して結果浮力不足．4540,5030はもっと速く脱調する．
試しにラップかけてみる？
SEL_LAP=LA1=LA2=Low
それでダメならモーター変えるか．

////////////////////
2015.05.10
脱調問題
ハーネスをUEWを短くして普通のハーネスを延長を試す&アームを補強．
->脱調頻度は減ったけど解消しない．実用レベルの頻度にはなったので保留
  もしかしたらPWM1%ステップにしているところをもっと細かくすると
  脱調しづらくなるかも(PWMタイマ周期変更)
  簡易的にSCコンデンサをでかくしてみる(0.47uF_100ms->1.5uF_319ms)
  ->だいぶ脱調しづらくはなった．脱調することはまだある
99%でも飛ばない．軽量化とPWM抵抗の変更
->R600を4.7k->3.3kに．
  まだ飛ばない．あとは軽量化．未使用のDIPピンを切る
  ->ALL99%でもやっぱり飛ばない．99%でもまだ上がってる感あるからR600を変えてみる
    よく見たら内部抵抗5.5kだ．1kでも99%で3.8Vにしかならない．
    3.3kの99%は2.83Vだからmaxの4.1Vに全然届いてない．
    ->1kで99%でも飛ばない．500Ωにしてもあんま変わんないからもうフル回転っぽい
      GWS4040,4540,5030購入して浮力アップを狙おう
      モーターを1404N 2290kvにする手もある．フレーム要変更．
      高いからペラを先に試す
筐体軽量化案
  足をデルタ型からスター型にする
  足自体を外付けにして飛んでる時は足なし

////////////////////
2015.05.09
筐体到着．幾つか修正漏れが合ったので次回修正．
基板・モータ等を移植して浮力確認したら浮く前にYpが脱調する．
重量自体が上がったのが原因？
脱調するのは修正漏れでアームが細くなってる所．
振動がデカいから脱調しやすい？モーターの個体差？

////////////////////
2015.04.30
なんか突然モニタソフトのグラフがうまく出なかったと思ったら，
グラフ側のデータをD1データが来ることを前提に組んでいて，
一時的に邪魔だからD1データをマスクしてたからデータが更新されていなかった．
これだけのことで3時間ぐらい潰してしまった．
-
QMLいじるだけでグラフ増殖できた．拡張楽だな．
グラフにタイトル追加．Y軸の中心を0とし，見やすいように太線に変更．
グラフレンジは-500〜500にしたけど，グラフごとにレンジをいじれるようにする？
→そのうちgraphオブジェクトでlinenodeの縦分割数・max/minを指定できるようにする
  getterでデジタル値を物理値に変換する

////////////////////
2015.04.29
タイマを80msに合わせる
->実測84ms周期．ほぼ合ってるからOK
バッテリのセル数でモータ回転がどんだけ変わるか確認
->波形を見ると3Sは60くらいで回し始めてる．2Sは40だから
  電源電圧でVSPのIC内抵抗が変わってる．
  3S:pwm50でVSP1.22V(最初だけpwm40でも1.5Vくらい出てるから，抵抗値が下がってく)
  2S:pwm42でもうVSP1.53V
  pwm_maxで回転数足りなかったら抵抗値を少し減らそう(4.7k->3.3k)
３Sで80ms/160ms/240ms/320msで全CHインクリメントしてどこまで脱調しないか
->86でlowbattになるまで80msでも脱調しない．
ホバーは320ms(4周期)で1upの制御にする．
姿勢制御は非制御範囲に幅をもたせる(±40くらい)
->十分浮力は出る．
  ただ急に浮力が上がったり下がったりする．手持ちで飛ばそうとするから？
  とりあえず自立する筐体と，暴走した時に手を触れずにstopさせる方法が必要．
  プロペラに手があたって血が滲んでる．
  加速度が一定範囲を超えたら停止．叩くと止まるようにしよう．
浮き始めるpwm値確認
->平均で全部が80くらいで十分浮力が出る．
バッテリホルダ割れたから筐体再作成
・バッテリのサイズが2S->3Sで変わったから調整
・足追加＋排気側を邪魔しないように足補強柱追加(気休め)
・サイズ制限でZ軸のp側プロペラガードが付けられないから削除
-
今後やること
・pi.cでpwmが55~-55なら符号反転し，さらに+なら+1,-なら-1する
(ただの反転だと閾値を行ったり来たりした時に無効値内に入って出て来られなくなる)
・ペラ反転時にバランスが崩れるのを補正するロジックを考える
・ジャイロの積分値で回転抑制(240msくらいでゆっくり)
・始動時の加速度を保持し，浮いたらそれを目標値にする
・control_cycle変数で時間管理(0~3)．回転数に応じて持ち替え
・加速度が範囲外になったら制御停止．叩いて止める
・ツール作成(グラフ増やす・データエクスポート)

////////////////////
2015.04.26
Ynペラが65くらいで脱調する？
->電源電圧が落ちて電流が足りなくなるっぽい．
  7V以上必要なICだからそもそも2セルじゃ無理？
全部のペラが75くらいでLowbatt(6.2V)になるっぽい．
無負荷で7.6V位なのにかなり落ちてる．リポって意外と内部抵抗デカイな．
３セルで試して行けそうならそれでいこう．
  ->３セルなら飛べる浮力は出たけど今まで45くらいで回り始めてたのが
    55くらいまで回らなくなった．
    更に回ってる状態でもいきなり浮力が増えるところがあって不安定になった．
    ドライバ側の入力は電源電圧によらず1.2V〜4.1Vなのでpwm26%〜89%に当たるはず．
    動き始めが40%だからIC側のリークが大きく，電源電圧によって変わってる？
    いずれにせよ３セルで再設計が必要．バッテリコネクタとR130変更
-
手で持った状態で飛ばすのは安定しなすぎて辛い．足つき筐体つくろう

////////////////////
2015.04.25
３軸合成で飛ばそうとしたらLowBattで止まった．
8bitADのはずなのに290までいってる．
よくみるとstaticで定義したaverageの前回値をクリアしてない．
このせいで前回の値(max255)を足し込んだ状態で/8してるから，286まではあり得る．
290になってる理由は？
-
ホバー仮実装したけどある特定のペラしか回転が増えていかない．
制御を最小単位に分解して１つ１つ確認していこう．

////////////////////
2015.04.20
3軸の合成ベクトルで飛ばそう．
■ホバー
全軸を45度傾けた状態でホバー．
-地面からの距離
  下3つの測距センサ全てが一定距離以上になるようにする．
  地面から以外も，全ての測距センサ値で汎用化して障害物から逃げる
-水平
  加速度センサの全軸の値が重力加速度/√2になるようにする
  (理論値181だけど実測151だった)
-回転(ロバスト性)
  加速度とジャイロの積分値を0にするように各軸のpwm値を調整．
  ゼロ点補正を始めにやる？
  過渡的な加速度はぶつかったとみなして機能停止
-制御スピード
  浮き始めはゆっくりコントロール．浮いたら速く．
-起動時
  最初は重力方向を確認して(裏返しONは動かさない)決め打ちの回転数に向かう．
飛ばし始めは手で持つ？台に置く？次フレーム作るときは足をつけてもいいかも
各目標値を定数で持つ．rotateとかも目標値に対する追従で実装．
ロジックはホバーと同じにし，
目標値との乖離と今の移動量を加味して制御スピードをコントロール．
関数構造
  pwm確認
  ホバー(2周期でpwm_1up)
  距離調整(2周期でpwm_1up)
  PWM書き込み
■移動コマンド
  動きを滑らかにするため最初の3サンプル(240ms)と最後の3サンプルは別制御．
  中間はリニアにインクリメント/デクリメント

////////////////////
2015.04.19
モータ全部を普通のハーネスで付け直し完了．
測距センサ全軸装備完了．
PWMのgetterが入れ替わっていて，間違ったCHの値を読んでたので修正．
Yp/YnをのPWMを99%にしても浮かない．結構アームのブレが酷いな．．．
重量180gがフルで回しても75gまでしか減らない，75g以上の軽量化が必要．
手っ取り早くプロペラ径を増やして浮力向上を試してみる．
GWS4025->GWS5043にするとフルで55g．全然浮かない．
測距センサ全部外しても55-44.4gだから10gぐらい軽量化してようやく浮く．
バッテリのせいで左右の重量バランスが悪いから，Z軸を回せば多少アシスト可能？

////////////////////
2015.04.12
手動の穴あけツール届いたからモータ取り付け用の穴開けた．
1mmの穴開けて1.2mmのタップネジ入れるとちょうどいい．
モータ回すとZ軸だけうまく回らない．
ワイヤーが長いから？
->筐体からモータ外して直接基板につけたら回った．
9V電源でやってるけど，7.4Vバッテリでやったら回る？
->関係ない
ワイヤの抵抗値でエネルギーが伝わってない？
->UEWじゃなくて普通のワイヤにしたら回った．これだ．

////////////////////
2015.04.05
筐体到着．
ナイロンだと思ったよりなよなよしてる．
4mm厚のところは十分強度が出てるけど，2mmのところは少し頼りない．
1mmのところは強度はほぼない．
■改善点
・2mm厚のところを3mmに変更
・pcbの穴径をΦ2.75mmに変更．部品に一部かぶってるから避ける
・プロペラガード/バッテリホルダを厚くする
・モータ固定のタッピン部分は仮穴開ける．超硬くてネジ入らない
・X軸の回転方向が弱すぎるから補強フレーム追加
とりあえずしばらくは接着剤と竹ひごで補強してだましだまし使おう．
プロペラガードは強度が全く無い．邪魔だから切る．
-
重量測定．
フル装備で110+7.4*6+31.5=185.9g
測距センサ外すと146.9g.これなら飛ぶ．
ただしフレームを厚くするから150gちょいとすると，結構ぎりぎりだ．

////////////////////
2015.04.04
モータ逆回転させようとするとマイナス値がセットできない．
どうもsetterの条件判定でdir<0が判定できてないっぽい．
signed charで0xECが入ってきてるから-20になってるはずなのに判定で棄却されてる．
dir<1にすると0まではif内に入るのに-1になると棄却される．
singedなのにマイナス値になってない？
->判定をdir>126にしたらif内に入った．やっぱりなぜかunsignedで処理されてる．
ただunsignedを前提に書きなおしたけどtimerにPWM値をsetしても反映されない．
もしかして8bitですらない？
->32bit見ても下位8bit以外は0だった．8bitでは扱われてる．
dir設定の後にtimer設定してはいけない？
->順番入れ替えても変わらず．
pwm値に0を設定するとバグる？
->-20からのデクリメントにしてもsetterでコケる．
最適化のバグ？int8を前提としたコードで最適化なしにしてみる．
->関係ない．
makeの出力見るとdutyが0以下になるなんてありえないぜって警告が出てる．
もしかしてchar指定をsigned charにすると符号アリになる？
->なった．まじか．この環境では[signedを付けない限りデフォルトでunsigned]らしい
-
逆回転次の浮力は正転時の半分より少し大きい程度．モータ2つで80gくらい．
pwm[%]と浮力[g]はほぼリニア．
リニア直線に対し，pwmがでかいほど浮力は少しずつ大きくなる．
-
UVLOを実装．205(7.2V)以下でpwm値を0にして"LowBatt"出力

////////////////////
2015.04.01
pwm値と浮力と電流の関係をプロットしてみよう．
とりあえずモータ1つで70gぐらいは浮力でそう．
2つで140gか．ギリギリだな．．．
pwmが40くらいで動き始めて，94で脱調する．
回すと音が結構うるさい．物バラを見たいけど続きは人がいない時間帯にやろうか．
浮力が一番出る脱調しづらいやつをY(重力方向への浮力)に配置しよう．

////////////////////
2015.03.30
モータpwmとdirection用のインターフェースを実装．

////////////////////
2015.03.29
10msで取得したデータを80msで平均してシリアル送信するようにしよう．
データ構造の設計ってコード書きながらじゃわけわかんなくなる．
とりあえず紙にイメージ書いてエクセルにメモしたけど，
もっといい方法ありそう．
とりあえず実装完了．平均値がQtで読み出せたからよしとしよう．
-
UVLO実装．バッテリ電圧の平均値が205より下回ってたらPWM値を0にする．
バッテリ電圧低下時の電源停止．
BVのAD値が205(7.2V)以下で確定しよう．

////////////////////
2015.03.28
zigbee通信のデータがたまにおかしい現象．
通信中に割り込みがあってデータが途切れるのかと思ったけど，
割り込み禁止しても改善しない．むしろ悪化．
Qtのモニタ側のバグだった．
1つは文字列の後ろn文字を切り出す操作で，[特定位置から19-特定位置]という操作を
していて，特定位置が19より大きい値だと変なデータになる．19にした根拠は不明．
19を配列の最大長(size関数で取得)にしたら改善した．
もう1つはreadAll関数でシリアル取得するデータ長が想定より短い場合があり，
1つのデータの中に3文字しか入っておらず，前のデータと連結しても
1つの情報にならないケースがあったため情報を生成できなかった．
前回データに連結するようにしたら改善した．
3つ目はそもそもreadAllにデータが入っていない．
これは改行までの1つの情報を割り込み禁止にして流しても改善されない．
原因がわからないが確率が低いので保留

////////////////////
2015.03.25
実装完了．とりあえずモニタグラフに加速度出たから配線はOKそう．
モーター系は筐体届いたら組み付けて確認しよう．

////////////////////
2015.03.22
注文後にバッテリホルダの天面がSTLに出てないことがわかった．
FreeCAD上で選択して天面が出るようにSTL出力すると，自動修正ではエラーが残る．
エラーの消し方がどうしてもわからない．
どうやらFreeCAD上で依存関係があるオブジェクトは勝手に結合されて，
結合前のオブジェクトをSTL出力時に選択すると2重に出力されてエラーが残るっぽい．
一旦依存関係を解いて(新規ファイルにスケッチのみコピー)全て依存関係のない
オブジェクトにした状態で全て選択->STL出力するとうまく行った．
ただ修正前のファイルでもう発注しちゃったから
とりあえずは現物見て治すか決めよう．
コミットファイルは修正後のファイルを入れることにする．
-
部品実装中．TOCOS DIPの場所ミスって加速度センサと干渉する．
足曲げてなんとか載ったけど，次基板変えるときは直そう

////////////////////
2015.03.20
問い合わせたら早々に回答が来た．
STL出力した時にZ軸のPCBホルダーオブジェクトを選択してなかったせいで，
厚みのない中空構造になっていたっぽい．
FreeCADで最低限のオブジェクトを選択してSTL出力
->netfabbで自動修正しエラーが無くなった状態でSTL出力したものを再アップロード
とりあえず作れる形になったようだ．

////////////////////
2015.03.19
注文した3Dプリンタ造形が[中空箇所があるため造形できない]と言われた．
問い合わせたらどこをどうすればいいか教えてくれるだろうか．．．

////////////////////
2015.03.18
netfabbを使うと自動でstlのエラー修正ができるっぽい．
何度かやってもエラーが消えなかった．
freecad側で，オブジェクトがなぜか結合されていて，
結合前のオブジェクトも含めてstl化していた．
stl化するオブジェクトを最小限に絞って
stl出力->エラー自動修正で造形可能になった．
サイズオーバーで作れないからZ軸のプロペラホルダーを2cmずつ短くした．

////////////////////
2015.03.16
DMM.makeに.stlデータ送ったら面が閉じてないから作れないと言われた．
.objでも.igesでも造形不可．3Dプリンタ用データのチェックツールがないと無理そう

////////////////////
2015.03.08
FreeCADスケッチで拘束が150超えるとフリーズしまくる．
ある程度小分けにパーツ作るとストレスなく出来ることに気がついた．

////////////////////
2015.03.07
PCBボード何も考えずにp板.comで頼んだけど，
調べたらユニクラフトってところが半値くらいでできそう．
ただデザインルールが違うから次基板変えるときに検討しよう．

////////////////////
2015.03.02
P板.comから修正依頼が来た．
viaを基板端ギリギリに打ち過ぎ，というのと，
繋いだつもりのGNDパターンが途中で切れてた．
(他でつながってたからエラーは出なかった)
修正して再送．ついでにモータの品名とR620の定数を修正．

////////////////////
2015.03.01
とりあえず形のイメージ作りのために2d図をラフに加減に書いてみた．(picture参照)
測距センサが流体の経路を邪魔してるからなるべく流速の遅いペラ中心に寄せたい．
その場合モータをネジ・ナットにするとモータの真裏にできないから，
モータをタッピングねじにしてナット取り付けスペースを削減する．
バッテリホルダは最低限の構造．
3Dプリンタでできるか不明だが，輪っかを２つ作って，
ケツを隣のフレームに突き当てる．
フレームは極力軽量化するため，ペラで移動する方に対する負荷を支えられるように
アーム断面の長辺を配置．
もちろんホバー状態でペラの吸気方向にアームを配置．
筐体厚は基本2mmで強度が必要そうなところは4mm．
この強度が妥当かどうかは不明．
基板に対して筐体は安く済みそうだからとりあえず作ってみる．
これからこの図面をFreeCADで作図していく．
プロペラの保護機構とアメンボの取付機構はその気になったらやる．

////////////////////
2015.02.28
とりあえずアートワーク完了
厚み1mm->0.6mmのFR-4で基板作ってみる．今回もp板.comで購入予定．
データアップロード完了．
今後の予定
  p板.comからの修正依頼対応
  部品表作成->不足部品手配
  3dプリンタ用に筐体再設計
部品表作成したらcommitしよう

////////////////////
2015.02.22
アートワーク中．kicadについてtwitterでつぶやくと即座に公式に補足される．こわい
kicadで部品番号をシルク出力したい場合，pcbnew上で部品番号が表示されていれば
[ファイル]->[プロット]->製造ファイル出力のオプションで
[モジュールのリファレンスをシルク上に出力]にチェックを入れる
(デフォルトで入ってる)とガーバーにシルクとして出力される
-
筐体はDMMの3Dプリンタを使ってみよう．
FreeCADでSTLデータを作る．チュートリアルやってみたけど慣れれば使えそう．
プロペラは排気の方が重要なはずだからアーム下に配置．アームが抵抗になるから
普通のクワッドコプターみたいに風を送る側にアームがあると不利なはず．
プロペラ機の場合は羽に空気を送って羽が揚力を生むからあの位置にある．
材料はナイロンが比較的軽いし，安くてサイズ制限が緩いからこれにしよう．
最薄部で1mmまで細かくできそう．比重は木材の1.5倍くらいだから，
フレーム重量の2.5倍と仮定しよう．
簡易プロペラ保護も付けたい．バッテリホルダも．
浮力が足りなかった場合は以下を試す．
測距センサ入れると150gくらいの浮力がなきゃダメそう．
以下なら200gぐらいでる？
1404N 2290kv　9.2g　ブラシレスモーター
http://www.hs-alfa.com/menew/motor/burasires/ds-1404N%202290kv.htm

////////////////////
2015.02.10
kicadいじり始めた．意外と使いやすい．
ライブラリとかデータが全部テキストだからgitとの相性が良さげ．
-
EEPROMはSMTパッケージで再選定，R1EX24512BTAS0I#S0がよさそう．
http://www.marutsu.co.jp/GoodsDetail.jsp?salesGoodsCode=238624&shopNo=3
-
DIP部品は未接続品の足をなくそう．
ソケット側を加工して，足を宙ぶらりんのままにすることでスペースを増やす

////////////////////
2015.02.08
FPWMで周波数を19.5kHz->39kHzにしたら少しましになった．
脱調するのは2.4V->3.4V,VBBのパスコン増やしても変わらず．
電源電圧ごとにmax浮力確認
7.4V  :52g
9V    :50g
11.1V :47g
電源電圧低いほうが限界が高いっぽい．
電子ばかりの上にモーター固定してるけど，固定方法によって浮力が変わる．
バイスで固定すると流体が阻害されるせいか30g程度しか出ない．
-
プロペラ同士の比較
プロペラ比較(9V電源)
MCF5035S  :45g
GWS5043   :42g
GWS4540   :43g
GWS4025   :54g
GWS0320   :37.7g(脱調しない！)
→4025で脱調しない設定にできないか？
固定方法を変えると68gまで浮力が出る．最低限浮くレベルまでは回せそう
-
WAVEMのバイアス変えてみる．
10k-9.5kにしてバイアス電圧を下げる→回りづらくなる．脱腸しやすくなる
9.5k-10kにしてバイアス電圧を上げる→脱調するのが早くなる．
→初期値の10k-10kがベスト
-
LA1,2とSEL_LAPでチューニング
ラップ無し
  進み角0   :65g
  進み角7.5 :64g
  進み角15  :68g
  進み角30  :77g  ※両方OPEN
ラップあり
  進み角0   :66g
  進み角7.5 :67g
  進み角15  :64g
  進み角30  :75g
→ラップ無し進み角30がベスト．
-
プロペラ逆転時の浮力比較
正転：75.7g
逆転：45g
→逆立ち飛行はかなり軽量化しないと困難．
少しずつ落ちながら一時的に逆立ちがいいところか．
-
この状態で 電源電圧確認
7.4V  :62g(脱調なし)
9V    :68g
11.1V :59g
→バッテリは2セル
-
軽量化案
・EEPROMをdip->sopに
・proボードのソケットを全品接続->使用ピンのみ接続に
-
浮くくらいはできそう．基板作ってみようか．
ドライバはもう変える気力ないから，作ってから更に浮力が欲しければ
モータとプロペラをいじってみる．
ドライバ変えるとしても次はFET外付けだろうな．
-
無償eagleの基板サイズ80x100mmだから入らない．
ライセンス買うか他のCAD試すか．．．ライセンスは2万くらい．
無償だとdesignsparkPCB,cadlusx,kicad,quadceptあたりか．
そのなかでmacで使えるのはkicadだけだがmac版はあんまり安定していないようだ．
選択肢がwindowsしかないっぽい．
designsparkはeagleライブラリが読み込める．
cadlusはp板.comでしか製造できないけどマニュアルが桁外れに充実してる．
kicadは流行ってるっぽい？ライブラリとかがテキストだからgitとの相性は良さそう
kicadのmac安定版が将来出るのを期待してwindowsで作っとくか．
とりあえずwindowsでチュートリアルをこなしてみよう．
仕事ならeagleライセンス買うけど，
時間を気にせず新しいところに飛びつけるのが趣味のいいところだ．

////////////////////
2015.02.07
デバイスTB6588FGと変換基板到着．0x基板を改造する
-
電源はDiを介さない
EN      Low             保護動作OFF
FMAX    OPEN            上限MAX
SEL_LAP OPEN            LAPなし.回ったら試してみる
IR      0.2ohmSR2012    0.5V/0.2ohm=2.5Aでリミット SR732ATTDR200F
http://www.chip1stop.com/dispDetail.do?partId=KOA1-1119950&mpn=SR732ATTDR200F
OC      10k0.1u(仮)     IRのフィルタ
WAVEP   10k1k0.1u(仮)   モータ位置検出
WAVEM   10k10k          調整すると起動しやすくなるかも
VSP     1.2V～4.1V
        4.7k/1uf
SC      0.47u(157ms仮)  ソフトスタート80msループ以下にする？
START   VSP=1V以上でL   起動時のAlign時間トリガ
IP      1u220kohm       Align時間152ms
OSC_C   100p            5.25MHz
OSC_R   20kohm          小さくすると早くなる？
FST     Hi,Hi           強制転流周波数12.7Hz
FPWM    OPEN            19.5kHz
LA2     L_チューニング  0度_通常転流時の進み角。静音性・効率
                        デカイと効率低下・トルク増加。モータ電流比較で決定
                        0で安定して回るなら0がいい
W       ショットキー
-
チューニング要素
・FPWMでPWM周波数上げてみる
・OCのカレントリミット用フィルタ定数
・WAVEPのフィルタ・モータ位相検出抵抗定数
・WAVEMのバイアス抵抗定数
・SCのソフトスタート定数
・IPのalign時間コンデンサ定数
・LA2で進み角調整
・SEL_LAPでラップ通電
-
50%でとりあえず回してみる→超低速で回る．
99%でやる→脱調して超熱くなる．TSDで間欠動作
デバッグしづらいからVSP入力を可変抵抗にしたら，50％でも脱調してた．
どおりで熱くなるわけだ．
LA1.2で進み角変えても特に脱調の改善はされない
VSP2.4Vで脱調するし，一気に上げると早めに脱調するから
SCの調整or出力微分値制限が必要．
脱調直前の浮力で41g．モーター+プロペラで5g*6=30g+基板80g,バッテリ30gとして140g
浮力は80g程度だから飛べない．脱調を回避しないと話にならない．

////////////////////
2015.01.29
ようやく評価ボード到着．配線ミスやダイパッドの接続が原因なら回るはず
→同じように回らない．
  モータとの相性？いずれにせよ手持ちの3種類のモータで回らないからダメっぽい．
  そもそも安定して数回転するモードでもたまに始動時の同期が外れて回らないから，
  安定して回るようになっても回り始めない位置があるのは避けられない．
別のモータ検討．とりあえず東芝TB6588FGで検討を進める．

////////////////////
2015.01.25
なんかプロペラGWS4025つけたら最初の100msは回った．負荷が足りなかった？
依然回らない時もある．ロータ位置による？100msでロック検知＋3.6secウェイト．
低速にしてみても100ms以上は回らない．
プロペラをGWS4025から5043にしてみる．
→回りづらくなった．
ロック検知は600ms以上停止しないとかからないはずなのに，
起動後100msで検知してるあたり異常な気がする．
解除もちゃんと3.6sの場合と即時解除の２種類がある．
アナログ的な要素？ダイパッドをGNDに落としてみるか．
→落としても変わらず．
FSをHにして高速回転モードにすると100ms回転→ロックがなくなって間欠回転になる
COM端子がモータPWM周波数にもろに吊られて振られてるから0.1u入れてみる．
→鈍りすぎて回らなくなった．
0.01u->100p->0で回りやすくなってく
comの抵抗をどんどん小さくしてみよう．
→4.7k->1k->500Ω...回らない
大きい側は？
→47kでも回らない．

////////////////////
2015.01.24
FG/RDを100kでプルアップしてみる
→かわらない
Lowスピードで回してみる
→回りやすくはなった気がするが間欠的に回る
この状態でCOMの定数をいじってみよう
  3.3k(間欠)->1k(間欠)->10k(ほぼ停止)->6.2k(たまに止まる)->4.7k(たまに止まる)
→手持ちの抵抗じゃ4.7kがベターっぽい．とりあえずこの状態で他を試す．
RD波形確認→すごいスピードでロックと復帰を繰り返してる
電流確認すると2Aop超えてそう．単純に電流不足で回ってない気がしてきた，
スロースタートできれば回りそうだけどそんな機能ないな．
とりあえず電流制限値を保証外領域まで上げてみよう．3.3k(2.2A)->2.4k(2.66A)
→スタート時に3Aくらい流れてその後ロックかかる，ぎこちなく周りはする．
  スタート時のロック解除が不自然．電流流しすぎるとロジックがおかしくなる?
  3.3k->3.1k(2.14A)くらいにすると不自然さはなくなる．が依然ぎこちない．
  いっそもっと絞ってみる．
  →ロックかかりまくる
  そもそもロックかかると3.6s間停止するはずなのに1msもしないで復帰する．
  たまに3.6sくらい止まって復帰する．２パターンのロックの仕方がある？
モータドライバにBEMSで不電圧がかかっているからDiで保護
→回転の仕方は特に変わらず
他のモータで回してみたけどやっぱりロックかかる．むしろ本命モータが一番マシ
評価ボード買って試してみてダメなら違うデバイスを探す．
  東芝TB6588FGよさそう．chip one stopに在庫ないけど取り寄せ出来そう．
  マルツに変換基板ありSOP IC変換基板 0.65mmピッチMAX48ピン用【SSP-64】
  もしくはモータにギヤかましてDRV10983で回す？
  →そもそもギアを使う前提のモータじゃないから見つからない．
  妥協してプリドライバ+FETという構成にして基板サイズ大きくするという手もある．
  TB9061FNG+FET
  DRV10963+FET
  TB6575FNG+FET
  ホール素子つければ選択肢広がる
モータドライバのデータシート，最大回転数が書いてないorわかりづらくてつらい．

////////////////////
2015.01.23
COM端子に接続している抵抗値をいじってみよう
10k->6.2k->4.7k->3.3k->1.5k->1k，だめだ，まわらない．

////////////////////
2015.01.22
接続完了．
霊によってうまく回らない．
少し回って止まる．もしくは50msおきにパルスを出してる→なんかリミットかけてる？
カレントリミットは3.6s毎にかかるはずだから電流ではない．

////////////////////
2015.01.21
IC到着したからテスト開始．
とりあえず0xボード上で部品をつなげる

////////////////////
2015.01.14
モータドライバ選定
DRV11873がよさそう．FSはH固定(high speed)で使用．
PWMとFRの２本*6chで制御．FR用のポート割り当てができるか確認が必要．
できればPA1,3,5,7,PB3,5を使いたいが，
PWMに内蔵タイマを使っているので設定できるか確認する．
PWM周波数は100kまでしか使えないので16bitタイマ調整timerClock=φ/4=62.5k
まずはI2Cに追加したmotor_initを元に戻そう
git checkout HEAD^ file1 file2 ...
で戻せた．
ポート出力をPA3で確認→Hが出たから大丈夫そう
デバイス購入しよう．

////////////////////
2015.01.11
設定した値が保持されているか確認
→sys_opt6/7/8/9:書き込めてるし止まっても変わらない
設定が正しいと仮定するとアナログ的要素で止まる？
→デカップリングコン100uF入れたけど変わらず．
クローズドループに入るときにスピードの急変が激しすぎて止まる？
→クローズドループに入れて，速度設定を300→511(max)にしたら回った．
  よく考えたら遷移してない状態では急変もクソもないから，
  クローズドループ遷移を入れない場合はしきい値に達すると勝手に止まるっぽい
  チューニングガイドにはしきい値で回り続けるって書いてあるのに．．．
max速度でも回転スピードあんま速くない
プロペラつけたらmaxスピードでもコアレスモータの時よりスピード遅い．
ドライバの限界が低すぎる(空冷ファン用？)から再選定が必要

////////////////////
2015.01.09
ステータス読み出せない問題．
同じ関数でgyroのwho_am_i読むとSIDが読めたから関数は機能してるけど，
driverからは読めてない．特殊な読み方が必要？
→gyroはリピートスタートで読みだしてるけど
  driverは一旦stopbit送ってから再スタートで読むっぽい
  変更したら読めた
status:ずっと0F→正常
faultCode:ずっと00→正常
モーターが止まるとSpeedCtrlが0クリアされてる
(2回目以降も普通に回ってるから関係ない)
EEPROM領域の書き込みビットを落としてみる→変わらない

////////////////////
2015.01.08
試しに電源電圧の低下でUVLOしてるか見てみたけど8V切ってないから違うっぽい．
全体的にはんだ舐め直したけど変わらず．
-
昨日の続き
→Opt7のロックを初期値に：かわらない
→Opt8のIPDクロックを10->01(初期値)にしてみる：かわらない
結局リミット値以外を初期値にしてもかわらない．
speedCtrl2のN/Aを0→1にしてみる：かわらない．
AdjMdを半周期にしてみる：かわらない
-
データシートあってんのか？電流制限の設定が逆とか．．．
電流制限・ロック系のしきい値を反転してみる？(ちなみにデータシートは最新だった)
とりあえずステータス読みだしてロックしてないか見てみよう
→status/faultCode:ずっとFF．動いてる時もロック状態？ロック検知無効だからか？
→SpeedCtrl1を読みだしてもFF．うまく読めてないっぽい

////////////////////
2015.01.07
試しにOpenClsしきい値を下げてみる
→25.6kHzだと半周くらいしか回らない．192kHzだと加速2にいく確率が下がる．
  しきい値に達して止まっているという感じではない
PWM周波数を50kHz->25kHzにしてみる
→回らなくなる．リプル電流が増えてリミットしてる？
極力初期値に合わせる
→CtrlAdvMdを整流時間固定に：ちょっと回る時間が伸びた気もするけど止まる
→OpenLoopランプ電圧を6Vcc/s→3→0.7：かわらない
→制御系数0.75→1：かわらない
→OPT5のロックを初期値(有効)にしてみる：かわらない
時間切れ．明日はOPT6から

////////////////////
2015.01.05
AlignTimeを短くしてOpenLoop加速を上げてみた．
OpenLoop加速2に移るタイミングで止まるっぽい？
OpenLoop加速2をいじっても変わらない．
Ktが小さい？
  →Ktを小さく設定するとOpenLoop加速2に移る確率が上がる．すぐ止まるけど．
    大きくするとより回らないから少し小さめで他のパラメータをいじろう
tdelayが合ってない？
  →実測300usくらい？3F->3C->3Aここがピーク->38->2Dで回りづらくなる
    49->4A->4C->4E->58->5A->5C->5Eどんどん悪くなる
    3Bいまいち->39いまいち．
Kt2.7では？
  →tdelay=3A加速2に行かない->58->5A->5Eだめだな．
    38->2A->1Aだめだった．
OpenClsしきい値を0.8Hzにしたら全然回らない．
ClsLp遷移を有効にしてもなにもかわらない．
N/Aの初期値が1だったけど0にしてた．直しても変わらない．
もう一度チューニングガイド読んでみようかな．

////////////////////
2015.01.04
ホビーショップアルファからモータが返送されてきたのでチューニング再開．
回らない状態の再現：Rm=0.387(0x2A),Kt=2.75(0x03)
  →回らないしAlignもキャンセルされてる．何が変わったんだろうか．
  →電流を1.6A→0.8Aにしたらすんなり回った．ある程度回転数が上がると止まるけど
    散々やって回る気配もなかったのに何が変わったんだろうか．
    ESCで1回回して特性が変わった？
ようやくチューニングが始められる．

////////////////////
2014.12.29
ホビーショップアルファから回答が来た．
普通に回るって．
年明けには返送されてくるからRm/Kt/OpenLoop電流閾値をもう一度調整してみよう．

////////////////////
2014.12.25
モータをホビーショップアルファで見てもらえることになったので発送，
結果は年明けかな？
とりあえず冬休みは他のことやろう．
結果来るまで開発一時中断．

////////////////////
2014.12.24
モータの9極分を絵に描いてalignと止まる場所をプロットすると，
どこからスタートしてもU相を通過できていない(V-W間で行ったり来たりしてる)．
これはモータ不良では？
各相の抵抗値は変わらなそうだから磁気回路故障？
→購入元のホビーショップアルファにメーカの出荷検査方法確認中
  回答来たら追加1個購入予定．もう1つのモータで試す？
  磁気回路故障だとしたらKt値が各相で違うはず．確認しよう
  →出荷検査してないしメーカー検査も知らない．送ってくれれば回るかは見れる
    との回答．どうするか．
    そもそも在庫が残り2個で，取り寄せ対応も不可と言われたうえ，
    他のネットショップに見当たらないから，
    6軸分モータを揃えられない．
    入手性のいい別のモータを探そうか．
    →hobbykingという海外ショップで買えるっぽい．日本の代理購入ショップもある
      http://agent.selfis.tv/hobbyking-guide
      壊れてた場合，これもう1つ買っていけそうならここで6個買おう
念のため機能やり残したOpenLoop電流閾値を下げるのを試す
→より回らない
違うモータ(A2212/13T 1000KV)
  実測値からRm=0.15
  Kt=293(5A)回りそう→440(5F)だめ→190(4D)回りそう→110(3F)回りそう
  →80.7(3B)回りそう→55(2F)もうちょい→40.3(2B)もうちょい→29.3(28)惜しい！
  →22(1C)もう一歩→18.3(1A)もう一歩→14.6(18)いい線いってる
  →11.9(0D)行けそう→9.17(0A)いいとこまで回る→6.42(07)まわらない
  →8.25(09)回らない→10(0B)いいとこまで回る→11(1C)もうちょい
  結果：9.17or10が一番良さそうだけど速度が上がると止まる
→モータドライバは正常っぽい．このモータは重すぎるからどうせ使わない．

////////////////////
2014.12.23
tdelayを0から変えていってみる．
0us,50,150,300,440,560,640,800,1040,1280,1600,2080,2400,3200,4800
→どれもあんま変わらん．
プロペラつけると慣性力が変わるから回りやすくなる？
→GWS0320じゃ変わらない．プロペラ先端に少し重りつけても変わらない
ググると3セル→2セルにして電流セーブすると回るって記事を見つけた．
今は9V_DCDCでやってるけど2セル=7.8Vでやったらアンプの動作電圧以下で動かない．
等価的にOpenLoop電流閾値を下げてみよう．何回かやった気がするけど．
→
それ以外だとモータ故障(断線/磁石のメッキ不良)も結構あるようだ．
コイル2つ分までは回ってるから可能性あり？
今までの経験だと部品不良の可能性はかなり低いけど．．．
他のモータ試す？変更パラメータはRm/Ktか．

////////////////////
2014.12.22
相抵抗を小さく設定しすぎ？電流があまりにも小さい，
1.6A設定なのに500mAもいってない気がする．
→0.46Ω・0.6Ω・1ΩにするとAlignがキャンセルされる．
  渦電流制限を制限なし(OFF)から最大値に変えたらどうだろう→効果なし．
tdelayを0からスイープさせてみる．

////////////////////
2014.12.20
設定パラメータを実測するために電流波形測定が必要．
本来なら電流プローブで測りたいが，高いので電流センサICACS714を使用．
-
いつものことだけど1発では動かなかった．
Alignが走ってないっぽいから下記手順で進めよう．
  →設定値の再確認
  →I2C通信波形を見てレスが来ているか確認
  →書き込んだパラメータを読みだして書込みできてるか確認
  →データシート再解読
→speed設定しないと回らないっぽい．指定したら回ろうとした．
極間を行ったり来たりして回らないから電流増やしてみたけど効果なし．
Ktをいじると傾向が変わるからスイープして回るポイントを探そう．
→Ktいじっても回るポイントがない．
  Kt264でPWM周波数を50kHzにすると回りそうになる．これが一番マシ．
関係しそうなパラメータ
  相抵抗
  Kt
  PWM周波数 とりあえず50k
  tdelay
  CtrlAdvMd
x OpenLCurr 上げると回らなくなる
x Op2ClsThr 上げてみる→11111
  OpLCirrRt
  KtLckThr
  Locken
  StAccel どっちが遅いか確認
  deadtime  最大にする(1111)
多すぎ．手当たり次第にやってられない．どうするか．．．
電流センサの影響が見えないので回るまでは外してやってみる．
→外力でモータ回してKt実測したら3mV/Hzだった．
  この状態でOpenLoop電流を1.6Aにしたら回りそう．．．で回らない．
  tdelay,Kt,Rmをいじったら少し変わるかも？明日やろう．

////////////////////
2014.12.20
デバイスドライバ実装開始

////////////////////
2014.12.18
ショットキーダイオードD1はブラシレスにすると電流足りなくなるから再選定しよう．

////////////////////
2014.12.17
0x基板に移植開始
TOCOS/加速度センサはDIPを直付けしちゃってるから外すのがクソ大変．
→はんだ吸い取り線であらかた吸い取った後にピンセットでグリグリやって，
  残った接続部分を割ると取りやすい．
AE-L3GD20を間違って逆接したけど繋ぎ直したら生きてた．運が良かった．
デバイスをDIP基板に載せた製品だから，
逆接しても死なないようにピン配を設定している可能性もある．
だとしたら気が利いてる．

////////////////////
2014.12.13
0x基板を改造してモータドライバ動作確認をしよう．
とりあえずSCL/SDAをつないでDIRにはPWM1で使っていたところをポートにして接続．
プロペラアダプタを買い忘れていたから追加購入．シャフト径2.3mm/3.175mm
スピンナーナット型コレットプロペラアダプター2.3mm
スピンナーナット型コレットプロペラアダプター3.17mm　
http://www.hs-alfa.com/menew/puropera/adp/prop_adp.html
モータでもう少し選択肢を増やす，電流2.8Aだからこのドライバでちょうど良さそう
浮力確認して見よう
HK-AP05 3000KV
http://www.hs-alfa.com/menew/motor/burasires/ds-HK-AP05%203000kv.htm
必要な39Ω抵抗もないから買おう．

////////////////////
2014.12.11
とりあえず翻訳完了
Hardware.odsにポイントだけまとめてコミットしよう．

////////////////////
2014.12.05
とりあえず評価環境を整えよう．
購入リスト
  ACアダプタ9V
    http://eleshop.jp/shop/g/g47H318/
  モータドライバDIP変換基板
    D028
  モータ
    http://www.amazon.co.jp/Turnigy-L2508A-3500-Brushless-Motor-ヘリ用ブラシレスモーター/dp/B00N8U8N1M/ref=sr_1_1?s=hobby&ie=UTF8&qid=1417787482&sr=1-1&keywords=L2508A-3500
    http://www.amazon.co.jp/gp/product/B00K7SAWH6/ref=ox_sc_act_title_2?ie=UTF8&psc=1&smid=A3IRMVGMZDEFGC
  モータ電流モニタ用センサ
    http://eleshop.jp/shop/g/gB3541B/
  変換基板
    SOP8-DIP8

////////////////////
2014.12.04
定格2Aのモータドライバだと回せないかもしれない．
無負荷時電流0.5AのA2212/13 KV1000で500gの浮力を生むのに
9Aとか書いてあるwebページを見つけた．
とりあえず実験はしてみるけどダメそうならラジコン用のESCを流用しようか．
どっちのモータも対応ESC30Aとか書いてあるからそもそも無理なのか？
その前にA2212/13 KV1000は内蔵抵抗0.09Ωとか書いてあるからドライバスペック外だ．
L2508A-3500は抵抗値が書いてない．試す価値が有るかどうか．．．
ただ1ペラ5Aくらい持ってかれたとして常時回る2ペラで10A，
ピークで20Aくらいいくのか？
バッテリ・コネクタ・配線に気を使わないといけない電流量だ．
-
ESC，制御方法はPWM入れるだけっぽいけど(周期．duty範囲は機種依存)，
逆回転ができない？逆転するには線を繋ぎ変えろという記述が多い．
逆転機能付きはRCカー用ならあるっぽい．(ごつい．重い．高い)
リレーでつなぎ替えてる人もいた．動作中に切り替えるのは危険すぎる．
やはり今のドライバICでどこまで回るかにかけるか．．．
電流増やせるドライバICあるけど制御pinが多すぎてマイコンリソースが足りない．
ダメならマイコンごと変更？その前にFET外付けで探そう．．．
TB9061AFNGとか良さそうだけど入手ルートがない．

////////////////////
2014.12.03
モータドライバ入手．fedexで普通に届いた．
翻訳続行中．モータに対する知識が無いため難航中．進捗6割．

////////////////////
2014.11.30
モータドライバは前に選定したDRV10983を使用する．
サンプルはTIサイトから入手可能だが企業のメールアドレスじゃないとダメっぽい．
通販サイトでは取り扱ってないっぽいけどいいドライバが他にないから
とりあえずこれで．
-
buckコンバータは外の回路で負荷を付けられるけど，付けないならLがいらないっぽい
→Lは嫌なのでデータシート通り39Ω抵抗で．
-
I2CorPWMorアナログ入力で制御するらしい．
I2C以外は回転方向やモータ回転数フィードバックなど信号以外に複数I/Fが必要
→I2Cで制御する．
  ただしSIDが固定なのでマルチプレクサでI2Cデータラインをスイッチして使う．
  マルチプレクサは以下が良さそう
  http://www.marutsu.co.jp/pc/i/170437/
-
データシート翻訳，集中力が続かない．

////////////////////
2014.11.29
モータ評価
180-47495を3セルリポで75%dutyで駆動すると無負荷時は5.79Vモーターにかかる
はずなのにモータ接続状態では2.83Vしかかかってない．
電流は500mA弱なのにドライバで3Vくらい消費
ON抵抗1Ω以下なのにざっくり6Ω相当のロス．
ドライバはさわれないほど熱い．浮力も28.8gとモーター１個分(34.6g)もない
プロペラ変えてどうこうなるレベルだとは思えないので切り捨て．
180-47495は直流抵抗実測0.6Ωに対し，GMS EM350は7.5Ωだから見込みあるか
と思ったけどほぼ同じロス．浮力．電圧降下があった．
→少なくともこのドライバで浮かせるのは不可能．
  ドライバは他にほぼ選択肢がなかったのでブラシレスに方針転換し，
  ドライバ周りの回路再設計を行う．
-
ブラシレスモータ候補
・Turnigy L2508A-3500
  http://atorie-m-m.shop-pro.jp/?pid=40780352
・NEEWER A2212/13 KV1000
  http://import.buy.com/ja/product/257537836/
  http://picworld.e-monster.jp/2014/07/23/マルチコプター-：-飛ばすまでに必要な物-モー/

////////////////////
2014.11.28
graphを複製して行きたいので，serial_ifとdataのインスタンス作成を
別クラスに分けたい(data,serial_ifも複製されてしまうので)．→ctrlクラス作成
QMLからインスタンスを作るからctrlとgraphを両方QMLから起こすようにする．
QMLからC++インスタンスのゲッターはQ_INVOKABLEで簡単に呼べた．
理解するのは超時間かかったけど．
とりあえずグラフが形になったからコミットしよう．
これからの流れ
・gridサイズをQMLからセットする
・グラフにラベルを追加
・グラフを複数表示

////////////////////
2014.11.26
lineNodeをOpenGLから読み取る形式だったのをgridNodeと同じ方法で2D描画する方式に
変更したらちゃんとグラフになった．
描画時は始点と終点の座標をセットする必要があり，同じ座標を指定すると
点になって見えないので，データ位置+1と-1の位置に縦線を引く，というのを
全時間軸で描画することでそれらしいプロット線が引けた．

////////////////////
2014.11.25
とりあえずグラフにデータを流し込めた．
グラフは画面下に行くほどプラスになるから，符号を逆にしないと
直感的なグラフにならない．
縦軸を1000maxに取って500を入れても中心線より少し下にグラフが描画される．
グリッド線もグラフ線もy=200のラインに引かれてるのに表示がずれる．

////////////////////
2014.11.24
モーターを手当たり次第に買ってるからそろそろ定量評価をしよう．
電流・電圧・回転数・浮力を測定し各モータ・プロペラでの相関を見る．
回転数は非接触回転計を使用．電圧・電流はADで見れるようにしているから，
物理値への変換さえできればいつでも見れる．

浮力はモータ単体を秤に固定しプロペラを回転させ，重量差を測定．
本体重量+モータ重量(+プロペラ)*6の重量を２モーターで持ち上げるのが最低限．
できれば３倍の浮力がほしい．
プロペラ逆回転で２モーターでギリギリ持ち上がるのが理想．

////////////////////
2014.11.23
MFTでクアッドコプター展示してる人と話したら，プロペラ浮力は機体重量の3倍ないと
使いづらいっぽい．
プロペラ到着したからモーターフル実装で重量maxを模擬し，浮力確認．
→プロペラ確認結果
  GWS　4025:ぎりぎり浮かない
  GWS　4540:同上
  GWS　5043:同上
結論：プロペラ経による浮力向上は負荷上昇と相殺されてほとんど変わらない．
→リポ3セルにして電圧上げる
http://www.kkhobby.com/SHOP/BT107.html
だめならモーター変更(かなり重い，トルク大，2セル用，ネットショップにない)
GWS EDP-300HC
http://robin.jp/SHOP/EDP-300H.html
http://www.sumamokei.com/ep1.html
ダメならブラシレス
(基板改版，軽量化のためマイコン変更も視野に入れる:mbed NXP LPC1768とか)

////////////////////
2014.11.22
チュートリアルのコードが断片的でそのまま打っても実行すらできない，
前提知識を要求してる文章っぽいから違う方法で基礎固めが必要．
QtQuick1.0の英語チュートリアル(11.20の上のURL)やってから
再度こっち(下のURL)をやるのがいい気がしてきた．
→英語チュートリアル短い上に最後の例で動作しない．
  すぐに2.0に戻ってきたけどやっぱりうまく動かない
-
もう面倒だからgraphのサンプルコード移植しながら作ってしまおう
→とりあえずマージしてsin波グラフとシリアル受信の機能をもたせられた．
  Widgetとqmlのウィンドウが両方でるから統合してデータにセンサデータを入れたい

////////////////////
2014.11.20
チュートリアルのQtバージョンが古くて全然動かない．
動くように修正しながら進める勉強法と，サンプルコードをコピペしていく勉強法
どっちがいいだろうか．前者は未経験にはハードル高い．
新しいチュートリアルを探してみようか．
http://qt-project.org/doc/qt-4.8/qml-tutorial.html
http://getting-started-qml-ja.readthedocs.org/ja/latest/chapter01.html
サンプルコードgraphはQtQuick2.0．2.0のチュートリアルがmust．
上のリンクは1.0だから下のリンクで良さそう．

////////////////////
2014.11.19
ブラシモータ到着
リポバッテリ2セル7.4Vだとギリギリ浮かない．．．くらいまで来た．
フル充電でプロペラサイズ上げればもしかしたらいけるかも．
ただモータ重量が結構あるから+4個のモータを載せて飛べるかは怪しいところ．
ブラシモータはトルクがでかいからプロペラサイズ上げても
回転数はそれほど落ちないと期待．
-
気になったのは，ブラシモータの場合回転数が電圧と比例しない．
5Vを切ると回転が完全に止まる．
制御を工夫しないとホバー軸方向以外のプロペラは回転数が低いから苦労しそう．
もしくはホバー軸以外はコアレスのまま，という選択肢もありか．
ただし軸交換してのホバーができないからいまいちか．
-
qwtは出来る見通しが立たないのでqt quickのscene graphで描画することにする．
とりあえずチュートリアルでqt quickの概要をつかむ
http://blog.qt.digia.com/jp/category/qt-quick-tutorial/page/2/
http://blog.qt.digia.com/jp/category/qt-quick-tutorial/
QtCreatorの中にサンプルコード[graph,customgeometry]があるから
これを参考に実装していく

////////////////////
2014.11.18
Qwtのインストールがうまくいかない
以下のとおりQtCreatorでビルドたライブラリとフレームワークを
QtCreatorパッケージ内にコピーしてinstall_name_tool -changeで参照先を
パッケージ内に変更したけど起動時に落ちる．
http://doc.qt.digia.com/qtcreator-2.4/adding-plugins.html#configuring-qt-designer-plugins-on-mac-os
参照先を変更しない状態ではプラグインとしては見つかるけど"失敗したプラグイン"に
分類されていて使えない．
妥協案としては違うパッケージを試す/チュートリアルにあるグラフで描く
QtQuickのSceneGraphがよさそう？

////////////////////
2014.11.16
データ取りこぼし問題．
根本的な問題．ターミナルでminicomで受信しても同じ事象．Qtのせいじゃなかった
→勘違いだった．マイコン側の送信カウンタのインクリメントタイミングミスってた．
  送られてくるデータはこぼさず拾えてる．
  ただし表示はかなり遅い．8秒間で80カウント行くはずが22までしかいってない．
  minicomなら80カウントいってるからQt側が遅い？
  emitでstoreDataに送る処理をマスクしても変わらないから
  readLine割り込みのペース，もしくはqDebugの出力(実際は格納できてる？)
  が遅いっぽい．
  →qDebugを最小限にしても出力ペースが変わらないからreadLineのペースが遅い
  →サンプルのTerminalExampleでは80カウントとれているからこの差分に鍵がある
    →readAllなら80くらい行く．readLineとreadAllに差があるっぽい
      →readAllで取得して改行ごとに自分で区切る処理にしたら
        とりあえず8秒で80カウントとれた．

////////////////////
2014.11.15
Qtでシリアル受信しているけどコンソール出力が明らかに遅い．
100ms周期で送ってるはずなのに1秒周期でしかとれてない．
80msでも1/10,2msだと1/2で取れる．
→負荷的に取れないわけではない
  受信が一定時間ないと無視するようになってる？
調べたらバッファクリアすると取れるっぽい記述があったけど
store後にserial->clearしたら取りこぼしが増えた．

////////////////////
2014.11.13
とりあえずコンソールに値を出すことに成功．
データを各パラメータごとに抽出して格納できるようにして，
クラスを分けたらコミットしよう

////////////////////
2014.11.12
ブラシレスモーターだと基板改版だけど，ブラシモーターなら今のまま行けるかも
この辺とか使えそうGWS EDP-50XC
http://robin.jp/SHOP/EDP-50XC.html
http://www.hs-alfa.com/menew/motor/burasi/ds%20gws%20edp_50.htm

////////////////////
2014.11.11
φ12cmプロペラアダプタ到着．全然浮力がない．
φ8cmと同じ重さでもそもそも回転数が上がらない．
φ8cmの方が浮力がある．
電子はかりで確認したらプロペラ1つで10gくらいしか軽くならない．
単純計算このモーターだと20gの筐体が限界．
軽量化の範囲ではないからモーターの再選定が必要．
将来的にカメラとか載せるかもしれないし．
軽量化路線ならこんなでかいモータドライバ・Gyro・加速度・I2Cバスコンは使えない
浮力計算は下記が参考になりそう
~~~~~~~~~
http://ameblo.jp/fullmetal-moon/entry-11330869139.html
静止推力（ｇ）＝（プロペラ径÷10）^3×（ピッチ÷10）×（回転数÷1000）^2×22
消費電力（W）＝（プロペラ径÷10）^4×（ピッチ÷10）×（回転数÷1000）^3×0.45
※単位：プロペラ径、ピッチはinch、回転数はr.p.m.、推力ｇ（グラム）、
        電力W（ワット）
ついでにプロペラによって得られるピッチスピード
（プロペラの直ぐしたのところの風速）の計算式は
ピッチスピード＝（P/10）×（N/1000）× 15.24　単位（Km/h）
~~~~~~~~~
マルチコプターのモーターはブラシレスモータが多いっぽい
ブラシレスモータはKV値というものがあり，巻線の巻数が少ないとKV値が高いらしい．
KV値が高いほど低トルク高速回転．コアレスモータも同じなのか？
だとしたら1.7Ωモーターはもっと軽いプロペラでは回転数高いかもしれない．
使わないから今更試す気はないけど．．．
-
モータドライバ選定
TI：DRV10983      ※バッテリを3セルに，本命
Hitachi：HA13605A ※ホール素子入りモータ

////////////////////
2014.11.10
Qtチュートリアル終わったからQtSerialPortのサンプルプログラムを参考に
ツール実装開始．
とりあえず受け取ったシリアルデータをコンソールに出すことを目指す．
-
電子はかりで重量測定．80gくらいっぽい．思ったほど重くない．

////////////////////
2014.11.08
筐体組み上げると机に置けないからスタンド作成．
アメンボは必要性が薄くなったから保留．
ぶつかった時の保護という意味ではプロペラの脇につければ十分な気がする．
-
モーター抵抗値違い比較
購入した軽いプロペラはモーター軸との接続がうまく行かず吹っ飛んでくから，
重いφ15cmプロペラと軽いφ8cmプロペラ両方で感覚比較．
3.3Ωのほうが1.71Ωよりもなんとなく風が来る気がする．
rpmを測定できれば定量比較ができるけどどう測ろうか．．．
ひとまずは3.3Ω品で本命プロペラ試してから考えよう．
-
プロペラ固定
購入したのはプロペラアダプタが必要なプロペラだったっぽい．
アダプタ在庫がsoldoutだからどうしたもんか．．．
とりあえず店舗に問い合わせてみるか．
→問い合わせたら2分で在庫ありましたメールが来た．早速注文．
  すげぇフットワークだindoor airplane．

////////////////////
2014.11.06
Qtでシリアル通信を実装するにはQextSerialPortとQtSerialPortがあるらしい．
QextSerialPort
http://d.hatena.ne.jp/wikuba/20120122/1327246038
http://kmst.sakura.ne.jp/joomla/topics/2010-06-25-03-48-23.html
QtSerialPort
http://doc-snapshot.qt-project.org/qt5-5.3/qtserialport-terminal-example.html
QtSerialPortが標準っぽい．日本語情報はほぼない．
まずはQtCreatorの使い方に慣れたらQtSerialPortでやってみるか．
-
QtCreatorのvimモード結構完成度高い．sublimよりよっぽどちゃんとしてる．
たまにカーソルが表示されなくなるけど．
-
初めてまともにIDE使う気がする．
癖が強いけど慣れればプロトタイプ作成は超早いかもしれない．
-
Qwtインストール方法．そのうち試す
https://www.youtube.com/watch?v=ZqFKwF6q7jQ
http://doc.qt.digia.com/qtcreator-2.4/adding-plugins.html
-
Qwtとserialport連携？あとで読む
http://www.qtcentre.org/threads/55707-Qt-with-qwt-qextserialport-unable-to-plot-from-serial-port

////////////////////
2014.11.05
コアレスモータはコイル抵抗が小さいほうが回転数もトルクもでかいっぽい．
抵抗小さい→インダクタンスが小さい→モーターとしては性能出にくい．
という理解だったけど違うっぽい．
インピーダンスの小さいモーター買って比較してみよう．

////////////////////
2014.11.04
モーター取り付けが鬼門．
つるつるした円筒形筐体が回転して上に引っ張られるから回転方向と上下方向の固定が必要
筐体側にガイドを作って接着剤で接着しテグスかなんかで補強する？
コアレスモータの表面があまりにツルツルだから超音波カッターで表面荒らしてみようか．
テグスで引っ掛けるところに少し凹みを出したい．
内部のクリアランスがどれだけあるかが気になる．
-
もう一つの課題が浮力．
プロペラは土曜に届くらしい．おそらく重すぎて飛ばない
	プロペラつけて浮力確認
		→軽量化検討(電子ばかりでどれだけ軽くなるか確認)
		→コアレスモーターインピーダンス違い品試す(そもそも仕組みは？)
		→サーボモータ検討(完全筐体再設計)		
-
アメンボ取り付けが地味に難題．
プロペラに干渉しないように強度のあるアメンボをつけようとすると曲がる強度のある針金．
重すぎるのでは？
1mm各の竹ひご３本束ねて使おうとしたけど配置も強度も話にならなかった．

////////////////////
2014.11.03
とりあえず筐体切り出し完了
ベニヤだと細いところが脆そう．接着剤とかで補強したほうがいい？
各軸の組み合わせ部分の精度が出にくい．調整に少し手間取った．
超音波カッターだと無意識に傾けて切ってたから断面が斜めだ．
気にしてたことだけど固定部が少なすぎて各軸の直角が出ない．グラグラ．
L型金具で直角を出そう．手持ちのやつで良さそうなのがあるからつけてみる．

////////////////////
2014.11.02
超音波カッター届いた．
2mm厚だと意外と切れない，押し込んでいくとベニヤが焦げる．
押し込まずに複数回で切るつもりで行けば割と切れるっぽい．
1mm厚までなら恐ろしいくらい切れる．

////////////////////
2014.11.01
リポバッテリー2セルでデューティ100%にしたらコアレスモータがオープン故障した．
5Vまでは壊れない確認ができたから5V上限で考えるか．
ちなみにリポ２セルの電圧範囲は7.2V-8.4V
-
TRIOでベニヤカットし始めたけど，ベニヤが脆いからボロボロになる．あと超うるさい．
当初代替案として検討してた超音波カッターのほうが良さそう．
穴あけはできないからそこだけTRIOに頼ろう．
超音波カッターが届くまで違うことをしよう．
→注文したら明日に届くらしい．恐ろしいなamazon

////////////////////
2014.10.31
φ150mmプロペラ全然浮力がない．重すぎて回転数が落ちるからφ80mmの方が浮力がある．
φ120mmを買って試してみるか．．．φ100mmで軽量のが在庫ない．
φ127mmで手持ちのφ8mmとほぼ同じ重さのプロペラがあるから買ってみよう．高いけど
http://www.shop-online.jp/eSlowfly/index.php?body=spec&product_id=643861&category_id=97881
-
筐体設計
測距センサをつけるためにモーター取り付け位置を釣り針型にしていたのを思い出した．
あとプロペラφ12が限界っぽいからそれを元にアーム長さ修正

////////////////////
2014.10.30
emacsのflycheckでinclude pathを追加してエラーを消そうといろいろ調べてたら
日付が変わってた．
flycheck-clang-includesでpath指定したらエラー消えた．

////////////////////
2014.10.29
macportsでQt5をインストールしてみたけど，web上のチュートリアルはQt4が多い．
実行すると色々エラー出てハマるっぽいからQt4入れなおした．
GUIで作れるツールが有るっぽいけど中身が見えなすぎてよくわからないから
しばらくはターミナル環境で慣れよう．
-
筐体設計：電池ホルダ用の穴あけるの忘れてた．
土曜にルーター届くから削りながら微調整しよう．

////////////////////
2014.10.28
processingでツールつくろうとしてたけどc++とQtを使ってみたくなったので，
自ら泥沼に突っ込んでみようと思う．
挫折したらprocessingに戻せばいいや．processingでもできるかわからんが．
-
C++の文法概要通読．
何がCの拡張だよ，ここまで拡張したら別物だろ．

////////////////////
2014.10.26
実基板を元に筐体再設計．

////////////////////
2014.10.25
基板届いた．見る限りミスはなさそう．
部品を実装していく．
-
買ったプロペラ思ったより重い．これが重いのかそもそもφ18cmだから重いのか．，，
コアレスモータじゃ高速で回せなそう．
実験したいけど穴径が違うから後日ゴム栓を購入してモーターに接続しテストする．
見込みなさそうだから15cm・18cmプロペラも購入して実際に回してみようか．

////////////////////
2014.10.18
部品表仮作成，東急ハンズで買う物は店舗行ってから決める．
来週基板が届くから電子部品系は発注しよう．

////////////////////
2014.10.14
DRCかけたらERRが100件超え．そんな気はしてたさ．．．
-
GNDが一本エアワイヤで残ってた．危ないところだった．
仕事だったら全ネット検図頑張ろうってなるけどテンション下がるからやる気にならない．
１時間くらい場当たり的にざっと見て発注しちゃおうかな．．．
-
3D図見てたら完全に方向ミスってるのに気づいた．
Z軸のプロペラ完全に横向いてる．．．
単純に横向けると固定方法が難しい，どうしたもんか．
→切り込み入れてはめ込むか．実機見ながら合わせれば行ける気がする．
  3D図面って修正する気力を削ぐな．．．

////////////////////
2014.10.13
後はGNDベタだけ，というとこまで来たけど，思ったよりスカスカだな．
あんなに苦労したのに最初に配置したあたりはぎちぎちだけど反対の基板端はスカスカ．

////////////////////
2014.10.12
信号線から優先して配線して行ったら電グラ線が通らないのでは？という気がしてきた．

////////////////////
2014.10.11
基板アートワーク開始
加速度センサのフットプリント間違ってた．危ないところだ．．．
-
当初の予定の70mmx70mmに載せるの不可能に見える．
→やり始めると割りと小さくまとめられそう，75mmx75mmくらいなら入りそう
→70mmx70mmに入るかも．アートワークのコツは思い切りと根気だという気がしてきた．
  DIP部品を半分ずらして表裏に実装するという裏技を思いついた．
  手ハンダだからこそできることだな．
  あと手実装だから基板ギリギリまで載せても捨て基板がいらないから楽だ．
  部品間も詰められるし
  そう考えると自動実装ってかなり制約が多いな，

////////////////////
2014.10.09
簡易グラフで見たけどうまく行ってないっぽい，
近似積分はブールの公式で実装してみたらそれっぽい値が出たけど，
距離は誤差がでかすぎて使い物にならなそう

////////////////////
2014.10.08
加速度から速度・距離の算出が鬼門．
速度は真値がよくわからんし，距離は誤差が積み上がってんのか間違ってんのかわからん．
グラフで出てくればイメージつかめるかもしれんからとりあえずグラフ作るか．

////////////////////
2014.10.06
モニタツールのwindowは左右2分割．右にセンサ値等を時間グラフで配置する．
右側は縦に4分割くらいして加速度・角速度・PWM・距離を表示．
加速度は速度・距離に切り替えて表示できてもいいかも．角速度は角度との切り替え．
左側には角速度と加速度を元に3Dオブジェクトを移動させたい．
-
書きながら作るのって難しい．紙の上で最初に関数分け考えてから作らないとうまくいかない

////////////////////
2014.10.05
角速度センサの実装を始めた．2バイト読み出ししようとしても，
値がHとLで同じ値になってる．加速度は勝手にアドレスをインクリメントしてくれてたけど，
こいつは同じアドレスから2回とってるだけっぽい．
とりあえず1倍とずつアドレスをずらして個別取得したらそれっぽい値がとれた．
-
データシートよく読んだらレジスタアドレスに違うアドレスを指定する必要があるっぽい．
1バイト読み出しの時は0x28で読むレジスタの場合，
2バイト読出したければ0xA8をレジスタアドレスに指定しなければならない．
やってみたら読めた．何だこの仕様．アドレスマップに書かないで字面でチョロっと
書いてあるだけだから完全に見落としてた．
-
EEPROMの実装は後回しにしてprocessingでツールの作成を始めようかな．．．
回路図の修正もしないとな．ツールとEEPROM動作確認ができたら基板起こすし．
-
processingでツール作成中．
なんかデータの合間にNULLがいっぱい送られてきてるからNULLを無視するようにした．
IDEのエディタが補完すらしてくれない
→PDE Xを入れたら多少ましになった．
  emacsでやりたいけど実行環境とエディタが分かれるのが面倒．
  ストレスが限界に来たら考えよう．
グラフ作成が楽だと思ってprocessing選んだけどあんまり楽でもなさそう．
Cで書くよりは楽なんだろうか．

////////////////////
2014.10.04
100Hzでセンサがデータためてるからその周期で読み出さないとダメっぽい．
10ms周期で空読みしたらそれっぽい値が出た．
→と思ったらZ軸は重力方向に200ちょい出てるけど
  X,Yは一瞬200ちょいになって安定すると30くらいに戻る．微分値みたいな出力．
  →Y軸を重力方向に向けると真下だと30位だけどちょっと傾けると200ちょい出る．
    明らかにある領域だけ値がおかしい．
    センサが壊れてるか，データフォーマットがバグってるか，
    読み込み時に化けてるか，送信時に化けてるか．．．波形見てみるか
    →読み込み時に化けてた．8bitシフト必要なのに4bitシフトしてた．

////////////////////
2014.10.01
ライトからリードの切替時のスタートビットはリピートスタートが必要で，
ストップビットを送ってはいけないっぽい．単純にストップビット送信をマスクするとバグる
リピートスタート時はSTAをセットしてから，前のデータの転送で立ったSIを
クリアして送ればいけた．
-
レジスタ設定→リードコマンドは送れてるっぽくてなんかデータは返してるけど，
加速度が0付近になってない．
2回めのリードではスタートビットが遅れておらず，
その後は加速度センサがLに張り付かせてるから何も送れてない．
→STOPビットの直前はNACKじゃないとエラーになるっぽい．AAビットを落としたらいけた．
-
データっぽいのは出てるけどZ軸は重力方向に200ちょいくらい出てるけど，
XYは値が30くらいからあんま動かないから取れてないっぽいor変な値が取れてる．
計算上は271LSBで1gだからXYも下向けたらそれくらい出るはず

////////////////////
2014.09.30
I2Cの初期レジスタ設定は送れた．
1回目のデータリードは信号は送れてるっぽい．
ただしW→Rの切り替えでストップビット/スタートビットを送らないと
リードコマンドが出せない．

////////////////////
2014.09.29
I2Cのデータ送信がタイミング的にかなりシビア．
SIビットを落とすタイミングはデータシートに厳密には書いてないけど，
SIDはスタートビット送る前にセットしないと送れない．
あとはSIビット落とすタイミングで取り込まれるっぽい
やっぱりデバイスドライバは波形見ながらじゃないと作れなくない?

////////////////////
2014.09.28
HWRとRDの接続が逆だった．なんか正しい波形が出てるっぽいけどwaitから抜けられない．
ENSIOを1にセットした後550us後にENSIOが1に落ちるはずが落ちてない．
→データシート見たらそれはパワーオンリセットの時だけ？
  とりあえずwhileでビジーループに変更
→何度やってもバイナリを書き込めないと思ったら2セルのリポバッテリが
  3.2Vまで電圧落ちてた(正常時7V以上)
  充電器につないでも接続不良になる．調べたけど買い替えしかないっぽい．
  この電池取り扱い難しすぎ．．．
  とりあえずACコンバータから使えるように改造しようか．
-
なんとか加速度センサからなんかの値をとれた．最初の2回だけ0b07,0b17でその後は0
加速度かけても0張り付きだからうまく取れてないっぽい．
明日以降はI2Cの波形見ながら解析していこう

////////////////////
2014.09.27
特に理由もなく，なんとなく開発が中断してた．
I2C実装中．
加速度センサの2バイトデータを受信する場合，
8bitずつしか転送できないI2Cではどうするんだろうか．
→仕様書見たら勝手にインクリメント・デクリメントしてくれるから
  2バイト連続読み出しでいいっぽい．ただしアドレスシフトはデバイスによる．
とりあえず実装して波形見ながら調整しておこう．
-
バッファモードは複雑そうだからバイパスモードで，と思ってたけど
バッファモードは例が細かく書いてあってバイパスモードの設定例がないからわからん．
バッファモードにしようかな．．．

////////////////////
2014.09.18
波形を見ると送信１回に対して何かをレスポンスしてるっぽい．
連続６回送信すると50ms周期でレスポンスを返してくる．
これがエラーになってるっぽい．
エラーの割り込みを分離して何回エラーが入るか見てみる．
→boot時に５回AD値連続送信後に１回ずつエラーが入ってる．
  多重割り込み時に発生？そもそもなんで送信に対しレスがあるのか？
  ToCoStick外してもレスがあるからDIPが返してるっぽい
TWE-Light DIP・ToCoStickを両方透過モードにしたらerrでなくなった&コマンド受信成功

////////////////////
2014.09.17
TWE-Lite-Rが届いたのでApp_UARTを書き込んだら普通に受信できた．
やはりApp_TweLiteでは普通のUART通信は未対応っぽい．
[超簡単！TWEアプリ]のあの絵は詐欺臭い．
-
zigbeeからの受信割り込みを実装しようとしたら，起動時に謎のオーバーランエラーと，
定期的に謎の受信割り込みが入る．
tocostickからなにか送ってる？プロンプトには何も表示されていない．

////////////////////
2014.09.13
I2Cバスコンのレジスタマップをlibre officeで作ってたらクラッシュして飛んだ．
自動保存から復元できたけど15分単位だったから最後の5分ぐらいは消えた．
こういうのでモチベーションが下がるのは何とかならないものか．．．
-
I2Cはとりあえず一番シンプルな割り込みなしのバイトモードで使ってみよう．
必要に応じて変更する．
データシート英語だし設定少し複雑そうだから難航しそうな予感

////////////////////
2014.09.12
結局UART専用アプリじゃなきゃUARTの通信はできないっぽい？
サポートにメールしたら
	標準アプリじゃUART通信できない？
		→手持ちのUART専用アプリだとできてるけど，，，(意訳)
という謎のやりとりになったからとりあえずTWE-lite r買って書き換えてみよう．
SDKはwindows版のほうが力入れてるっぽいからwindowsでSDK入れて書き込みしよう．
App_UARTを見てから必要に応じて改造．
TWE-Lite Rが届くまではI2Cバスコン側の実装を進める．

////////////////////
2014.09.10
zigbeeに波形入れると出力電圧が1V弱/GNDの波形になる．
zigbeeの設定品をいろいろ試したがどこも問題なく，結局3.6Vが出ていないことがわかった．
探っていくと加速度センサのJ2をショートしていたことで
アドレス設定品が3.6Vになっていて，そこをGNDにするつもりで回路でGNDにしていたから
3.6V-GNDショートになっていた．
多分自分でショートさせたんだろうけど，なぜJ2をショートしたのか覚えていない．
-
とりあえずzigbeeでシリアルを飛ばせるようになってminicomで受けられたっぽいが，
すべて文字化けしているし，10sec間隔でデータを送っているはずなのに，
1sec間隔で文字化けした何かが出る．ボーレート設定が怪しいがzigbee側もminicom側も
問題なさそう．
→TOCOSTICのデフォルトが115200bpsっぽい．
  これを38400bpsにすれば動きそうだけど変え方がわからん．
→結局分解してBPSをGNDショートしたら38400bpsで起動メッセージが出た．
  ただデータが1sec周期で謎の16進数.
  →ボーレートはコマンドで設定できる方法があるっぽい．明日確認しよう．

////////////////////
2014.09.09
熱対策：
コアレスモータと直列にコイルを入れることでリプル電流を抑制し，
発熱を抑えることにする．
16bitタイマの250kHzのPWMだと22uHで許容範囲(暖かい？くらい)に収まりそう．
8bitタイマの31.25kHzだと100uHくらいが良さそう．
22uHはラジアルタイプが秋月にないから47uH[LHL08NB470K]，100uHは[LHL08NB101K]
-
zigbee実装しようとしたら今までSCI0だと思って書いていたものがSCI1だった．
どこで間違えたんだろう．

////////////////////
2014.09.08
PWMでデューティ50%でほぼ静止状態なのにモーター超熱い．
周波数あげたら良くなる？
250kHz->500kHzにしたけど30秒で触れなくなる．
250kHzだと15秒位で限界だからマシにはなるようだ．

////////////////////
2014.09.07
AD変換方法の検討．scan modeに単一と複数を同時取得するモードが有る．
しかし複数ch同時でも0~3,4~7の2回に分ける必要がある．
複数同時は常にスキャンし続けるため電力的には不利．
単一は必要なときに読みに行くためAD変換が終わるのをループで待つため時間的に不利．
以上を踏まえ以下の3案を検討
○案1	スキャンモードで
	0~3ch読み取り後4~7chを設定し完了フラグを待って読み取り
◎案2	単一モードをループで待って全ch読む
△案3	スキャンモードで
	奇数回目の10msタイマー割り込みで0~3chを読み取り
	偶数回目で4~7chを読み取り
案2で時間的に間に合わなければ20msタイマにして時間を伸ばすのが良さそう
また，10bitADだが上位8bit->下位2bitの順で読み出すため，
上位8bitで事足りるならそれだけで良さそう．
精度はそんなにいらないので上位8bitだけ取り出すことにする．
-
ADCのデバイスドライバ実装中．何度やっても0しか出ないと思ったらレジスタ設定の
上位と下位を逆にしていた(ex 0x0f->0xf0)．
AD完了をADFでなくADSTで見ていたのでうまく行かなかったようだ．
直したら測距センサの値が正常に出力された．

////////////////////
2014.09.05
リポバッテリー到着，基板側のコネクタはS3B-XH-Aが良さそう．
ユニバーサル基板上にひと通りのデバイスを載せてデバイスドライバを作る．(0x基板)
モーターと測距センサはとりあえず1chずつ．
意外とユニバーサル基板ってはんだづけしづらいな．．．綺麗に配線できない．
とりあえず配線終了．シリアルから文字列が送られてきてるし3.6Vも出てるから
これからデバイスドライバを実装していく．

////////////////////
2014.09.01
バラックボード実装中．2.54mmピッチのユニバーサル基板に乗せるとかなり面積食う．
モーターと測距センサは動作確認できればいいから1chずつ．
-
やはりネックはプロペラの浮力．
以下のプロペラ15cmと18cmのセットを買って試してみよう．
http://www.rubberpowerplane.com/pg12.html

////////////////////
2014.08.27
部品実装完了．Proボードでソフト動いた．
ここからボード外の回路をテストしていく．
足りないもの
・pinヘッダ2x20
・pinヘッダ1x20?
・pinソケット2x20
・フラックス(0.65ピッチ実装用)
・リポバッテリー2セル
-
PWM実装・AD実装をそろそろ始める

////////////////////
2014.08.24
Proボード届いたけどh8とDRAM以外部品が実装されていない．
Proボードってそういう意味だったのか．とりあえず手持ち部品で実装していこう．
まずはaki-h8_3069fで作ってたソフトをちょい変して少しずつソフトを作っていこうか．

////////////////////
2014.08.23
よく考えたらデバイスドライバの初期化関数は1度動いたら変更しないから
テストいらないのでは？リファクタリングする場合以外は．
いや，異常系のテストしたい場合はいるのか．．．
思ったよりCppUTest使いこなすのに時間かかりそう．
イニシャライズだけ先に実装するか．
...なにか大きな勘違いをしていたかも．CppUTestってh8上で実行できない？
パソコンでコンパイルしてもh8向けのバイナリでテストが成功するとは限らないし，
h8上で関数テスト関数を実装してリリース時にはmakefileで分離できるようにしたらいいかも
ということでとりあえず実装開始してテストがしたくなったら
test関数上で分離できるように実装しよう

////////////////////
2014.08.16
Proボードが届くまで少し時間がかかりそうだからTDDを試してみたい．
[テスト駆動開発による組み込みプログラミング]を試して，
その後テストコードをソースに入れ込む．しばらく開発が停滞する．

////////////////////
2014.08.15
ZigBeeのUARTボーレートは115200bps/38400bps．
h8の設定では115200は誤差が大きすぎるため38400で使用．BRR=19
minicomで数字がバラバラ表示されても意味わからんから
PC側でグラフィカルにログできるツールが必要．
Arduinoのお陰でサンプルコード結構ありそう．Processingって環境で作りやすいらしい．
グラフ表示・数値保存・数値再生・3D表示(加速度・角速度似あわせてモデルを動かす)
-
測距センサは角度分解能が低いから死角が多い．
筐体の正面を決めて最も障害物が近い方に正面を向ける．
動いてれば回転するから死角が減らせる．
-
パラメータって何があるのか具体的に考えてなかったからちょっと考えよう．
・PWM設定値*k=移動加速度or角速度(静的)
	6軸組み合わせ?2^6=64パラ?6パラのベクトル演算で行ける？
・PWM変動値*l=収束時間or単位時間での加速度変動(動的,伝達関数)
	6軸組み合わせ?2^6=64パラ?6パラのベクトル演算で行ける？
・PWMリミット値(モータ保護)
・電流リミット値(モータドライバリセット)
・接近回避しきい値 6軸
-
移動座標をそのまま扱うのは難しそうだから加速度/角速度ベースの制御が良さそう．
ある点からある点へ移動させるには加速度値はsin波を描くようにしなきゃならない．
PWMは定数lの遅れがあるからその分を補正する必要がある．
lは単位時間毎(100ms?)で分割して持ったほうが良さそう．
ちなみに10ms周期で加速度等を観測し100ms周期でPWMを調整する予定
-
イニシャライズコマンドでk,lを自動取得したい．
重力方向によってパラメータが変わりそう？
重力加速度を定数ベクトルとして持っておけばベクトル演算で行ける？
まずはZ軸固定でやって，その後パラメータは考えよう．
-
空間移動は座標->距離->到達時間->sin波(加速度-時間)マッピング
	->100ms間隔でのPWM値マッピング
到達時間は単純な1次関数にはならないので注意が必要
(近距離では遅くなる,遠距離では1次関数に近づく)

////////////////////
2014.08.14
zigbeeのRSTはフローティングで解除されるのか？記述がないけど接続例ではOPEN．要実験
-
バスに抵抗入れて保護するのは抵抗アレイに変更．さすがに多すぎ．
BCN164AB102J7LFなら3216で４素子(1k)．マルツで買える
-
そろそろ部品表作らないと．混乱してきた．
-
inventor fusionで3D図面書いてたらフリーズして書いてたデータ飛んだ．
こまめにセーブしよ．
骨格書き上がったけどモーターとプロペラないとわからんな．

////////////////////
2014.08.13
電源入れた直後はPWM出力できないから電源電圧がモーターにもろにかかる．
ドライバの出力を切れる回路を追加する．
-
電力効率の計測のためにBAT電源電流をモニタしたい．
作動増幅？電流が一定値を超えたらモータ出力を止める？(突然の自由落下)
良さそうなICはある[LT6106CS5](検出0.02Ω-0.2W,入力200Ω,出力10kΩ)
検出抵抗はCRL1206-FU-R020ELF(RSコンポーネンツ3216サイズ)それ以外は1608で適当に
http://akizukidenshi.com/catalog/g/gI-07300/
非常時だけならヒューズを入れればいいか．
リセッタブルヒューズってのがあるらしい．熱で物性が変わって抵抗値が急激に増加する．
http://jp.rs-online.com/web/p/resettable-surface-mount-fuses/6917597/
↑この辺試してみる？7.5x5.5くらい．MF-SM300-2
-
ProボードCN1,CN2の接続はLANボードと全く同じ．さすが秋月わかってる．
-
電源電圧上がったから逆接保護Diいれるか．リークは気にならないからショットキー
[SR54F]
どんどん面積が増えてる気がするけど載せてから考えよう．

////////////////////
2014.08.12
測距センサが5V動作品(4.5~5.5V)だった．なぜ気づかなかったんだろうか．
とりあえず3.7Vで動作確認．
→黒線が5V入力・赤線がGND入力だった．逆接して壊した．死ね．
-
LiPoバッテリ実測4Vちょい出てる．加速度センサの定格が3.9V,動作maxが3.6V．
3.3Vレギュレータかませる?Zigbee,I2Cバスコン,Gyroも3.6まで．
DRAM,NOT回路4.5~5.5
Lipo直列にして6~8Vを5V/3.3Vドロップ．モーターはBatt直結PWMで制限?実力行ける?
多電源だとレベルシフタが必要．電源電圧を極力近づけて直接やり取り．
定格超えるけど実力行ける？1.5kくらい抵抗入れて何とかなるかも．．．
レギュレータ[NJM111000F1]
Batt:	モータドライバ
4.5V:	DRAM，NOT,マイコン,シリアル,測距センサ,モータドライバ(I/F),EEPROM
3.6V:	Zigbee,I2Cバスコン,Gyro,加速度
LiPoは2セルのモジュールが売ってる．充電器とともに購入
http://www.kkhobby.com/SHOP/BT167.html
-
I2Cのアドレスがかぶっていないことを確認
デバイス	I2Cアドレス
加速度センサ	0x53(L)		or 0x1D(H)
Gyroセンサ	0xD5 & 0xD4(L)	or 0xD7 & D6(H)
EEPROM		0x90 & 0x91(LL)	or 0x98 & 0x99(HH)
問題なさそうなのですべてL接続で使う
-
角速度センサはFIFO持ってるけどポーリングで10ms周期でとるからBypassモードで使う
-
プロペラはこれでも良さそう6x4Eは6inchでピッチが4inch
http://www.kkhobby.com/SHOP/PP031.html

////////////////////
2014.08.11
コアレスモータをLiPoバッテリでフル回転させたけど，8cmプロペラ2個で飛べるとは思えない
18cmプロペラで飛べるか確認→ダメならモータ変更
なお，逆回転は問題なし
-
筐体構造検討，手書き図面作成,とりあえず試作してみる
-
アメンボどうやってつけよう

////////////////////
2014.08.09
回路図作成のため部品ライブラリを作成する
		symbol			package
マイコン	h8/3069f		h8/3069f_pro_board
DRAM		M5M417800
マイコンボード	h83069f-pro		基板
モータDr	TB6593			基板
LiPoBatt	LiPoBatt		コネクタ
モータ		MK07-3.3		コネクタ
測距センサ	GP2Y0A21YK		コネクタ
zigbee		TWE-001L-DIC-WA		基板
Gyroセンサ	AE-L3GD20		基板
加速度センサ	ADXL345			基板
シリアル変換	PCA9665PW		基板
EEPROM		24C512			24C512
Not回路		TC74ACT14FT		基板	
-
LANボードとProボードはDRAMのpin配が違うがCPUとのつなぎは同じなので
ソフト変更不要のはず．
クロックは25MHzが標準なのでLANボードでテストするときに付け替えておく
-
プロペラ思ったより小さい．飛びそうにないから以下の15/18/21cmを試す
http://www.rubberpowerplane.com/pg12.html
紙を各デバイス・基板サイズに切って基板サイズ予測->プロペラサイズを感で決める
→最終的には70x70mmに収まりそう．
  そこそこの重さになりそうだからプロペラは18くらいか．
-
UART-シリアル変換は在庫がなさそうだからI2CバスコントローラPCA9665PWを使用
http://www.marutsu.co.jp/ichiran/?SHO=011811
NICと同じ方法でアクセスできそう
-
モータドライバはh8Pro基板の下に実装．SMTを直で(DIP変換基板にしない)．
NOT/I2C/ACCもPro基板の下に入れられそう．
ACCは軸中心に置きたい．Gyroはどこでも．ビス付近の方が振動しなくていい．
Zigbeeアンテナはプロペラと干渉しないように注意

////////////////////
2014.08.06

買い物メモ
■回路
モータドライバ	[【TB6593FNG(O.EL)】ブラシ付きモータドライバIC ]
		[【D020】変換基板(20ピン・SSOP/SOP・5枚) ]
マイコン	[aki-h8/3069FマイコンボードDRAM付 Pro用]
バッテリー	[リチウムポリマーバッテリー3.7Vx1](USB充電可能なもの)
		コネクタ[1.5mm ピッチJSTベース付きピン 2 ピン 10個セット]
測距センサ	[GP2Y0A21YK]_x6
zigbee		[TWE-001L-DIC-WA]_x1(37x19基板)_デバッグ用に2個購入
			(PC側は[TWE-Lite-USB])
3軸ジャイロセンサ[AE-L3GD20]_x1(12x12基板)
3軸加速度センサ	[ADXL345]_x1(19x14基板)
シリアル-SPI変換モジュール
		SC16IS750搭載I2C/SPI_x1(12x14基板)
		在庫がないのでR1350N搭載ジャイロシールドを購入し改造
EEPROM		[24C512]_x1(1.0x0.9)
NOT回路		[TC74ACT14FT]
変換基板	[TSOP18ピン変換基板AE-TSOP-2]
紙基板
ユニバーサル基板
	両面スルホール・ガラス・ユニバーサル基板Ａタイプ
	２．５４ｍｍピッチ（１５５ｘ１１４ｍｍ）
■可動部
プロペラ	[CF3222ADP,U80N2]_x6
			(ギヤユニット[GB05など])
モータ		[MK07-3.3]_x6
■筐体(上記入手後ハンズで購入)
t=2mmシナ共芯合板
Dremel万能ルーター(TRIO)
モーター固定用Oリング
プラスチックなべ小ネジ

////////////////////
2014.08.03
モータドライバ[TB6593FNG]よさそう．秋月で買えないけどマルツにはある．
ピンピッチが細かいので変換基板をかませる
[【TB6593FNG(O.EL)】ブラシ付きモータドライバIC ]
[【D020】変換基板(20ピン・SSOP/SOP・5枚) ]

////////////////////
2014.08.02
モーターが逆回転できるか試さないとまずい．
-
モータードライバ3~3.7Vで動くやつある？TIのDRV8832が良さそう．秋月で買えるし．
DRV8830ならI2Cで指定できる．6chあるから通信ディレイがデカそう．却下．
PWM入力は反転して２入力にしないといけない．NOT回路6個入り準備[TC74ACT14FT]
ダメだ，データシート見るとPWM入力じゃなくて，
H-L入力の時に定速正転，逆で逆転，ブレーキ，惰性の4パターンしか出せないっぽい．
速度はVset端子電圧で決まるから，DA出力+正・逆をポート制御？あまりにも．．．
[TB6552FN/TC78H610FNG]ON抵抗がかなり高い．[TB6593FNG]いける？要確認
-
筐体は厚紙やパルプ．ベニヤ等の素材を切って試作．最終的には3Dプリンタ？
東急ハンズで見たところ2mm厚シナ共芯合板が良さそう．塩ビ板より軽くて曲がりにくい．
万能ルーターってやつで切れば試作レベルの加工はできそう．要実験．
モーターはゴムのOリングで切込みを入れた合板と巻きつける．
合板同士はプラスチックなべ小ネジで組み付け．
-
最終的にカメラを載せるかも．最初は載せない．
まずは形にすることを優先し，難易度の高いものは後回し．重いし．
-
最終基板はEagleで書く．(macでできる&オープンソースハードの定番っぽい&100x80に収まる)
暫定回路図もそれを見越してEagleで書く
h8は変換基板に載せる？FLASH書き換え回数増えるとデバイスだけ載せ替えたいかも．

////////////////////
2014.07.30
クワッドコプター購入．[4ch マルチコプター R/C スパイダー 赤]
プロペラが意外と小さい，が，かなり軽い．本体の筐体も無駄がなくて軽い．
軽さが一番重要そう
FR4,2層貫通基板
各モーターには2本の線が接続されている.
1本は共通(電源),マイナス側をNchFETで引っ張ってる
NchFET(BSS123?)x4でモータ駆動
無線2.4GHzトランシーバはA7105,基板上にアンテナパターンを形成.
リポバッテリーは3.7V240mAh,モータ駆動も3.7Vでしてる．
モーターはコアレスモータ？小さくて良さそう．
モータドライバでPWM制御(FETだと逆回転できない)
直結は効率が悪いらしいからギヤユニットをかませて作る?
	indoor airplane world e-shopで購入可能
	コアレスモータ[MK07-3.3]
	ギヤ[G209-071,G260]ギヤユニット[GB05など]を使用．実験して必要に応じて使用
	プロペラ[CF3222ADP,U80N2]
	電源[リチウムポリマーバッテリー3.7Vx1]
		マイコン直結(3.3V動作可能)
	マイコンはボードだと重いので[h8+QFP/TQFP100ピン変換基板]+紙基板

////////////////////
2014.07.29
自立飛行なら近接センサが必要
各プロペラに1セットずつ外側に向けて配置
シャープ測距モジュールが使いやすそう[GP2Y0A21YK]
6軸を監視しないと6軸移動できる意味が無いので3軸加速度+3軸ジャイロを載せる
秋月のラインナップから下記部品が買いやすい
EEPROMにパラメータを記憶する→自己学習みたいなことができるか.
DRAMにセンサデータを格納し，モニタしながら制御方法を検討

////////////////////
2014.07.28
着想：
H8マイコンを利用してラジコン的なアクチュエータを制御する物を作りたいと思っていた．
タイヤはありきたりだし，水に入れるのは実験が面倒なので空を飛ばすのが良さそう．
クワッドコプターは結構製品化されて性能が出ているが，もっとプロペラを増やして自在に動かしたい，

構想：
全軸(6軸)に移動可能にする．シンプルに考えるとXYZとそれぞれの回転方向で2個ずつプロペラをつけ，
全12個を使用すると良さそうだがあまりにも多い．
例えばZ軸移動とY軸の回転方向は共通のプロペラでできそう(X軸端にZ軸を中心とするプロペラを2個)．
そこで計6個のプロペラで6軸移動が可能になりそうと考えた．
デバッグや指示出し用に無線で双方向通信ができると便利．
Xbee(zigbee?)が秋月にもあって使いやすそう．
XbeeエクスプローラUSBドングルってのでPCから拾えそう

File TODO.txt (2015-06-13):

====================
TODO:
・モーター制御実装
・回路図バッテリコネクタ3Sに変更，R130を10k->20kに変更
・基板のTOCOS DIP位置修正
・モータ端子に1Ω挿入(UVW全てに)
・4.5Vレギュレータ変更(AZ1117H-ADJ)
  C113:22uF,R111:3.9k,R110:1.5k,R112:OPEN
・C4x6をOPEN->0.01uFに変更
・C6x2を0.47uF->1.5uFに変更
・基板のデザインルールをユニクラフトに対応
・ランドの周囲にレジストかぶせて強度UP

====================
ツール
  コマンド送信ボタン実装
  グラフごとにレンジ指定できるように変更
	テキスト保存/テキスト再生/グラフ表示/3D表示の4タイプ選択
	・加速度情報x3
	・角速度情報x3
	・PWM出力値x6
	・距離情報x6
	・電源電圧
	・電源電流
	パラメータを書き込み

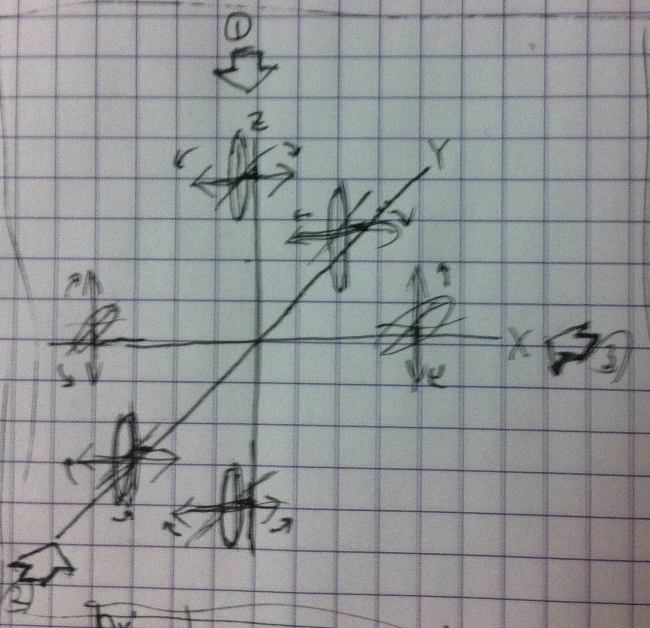
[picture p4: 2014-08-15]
devlog/picture/2014.07.28_layout-image2.JPG

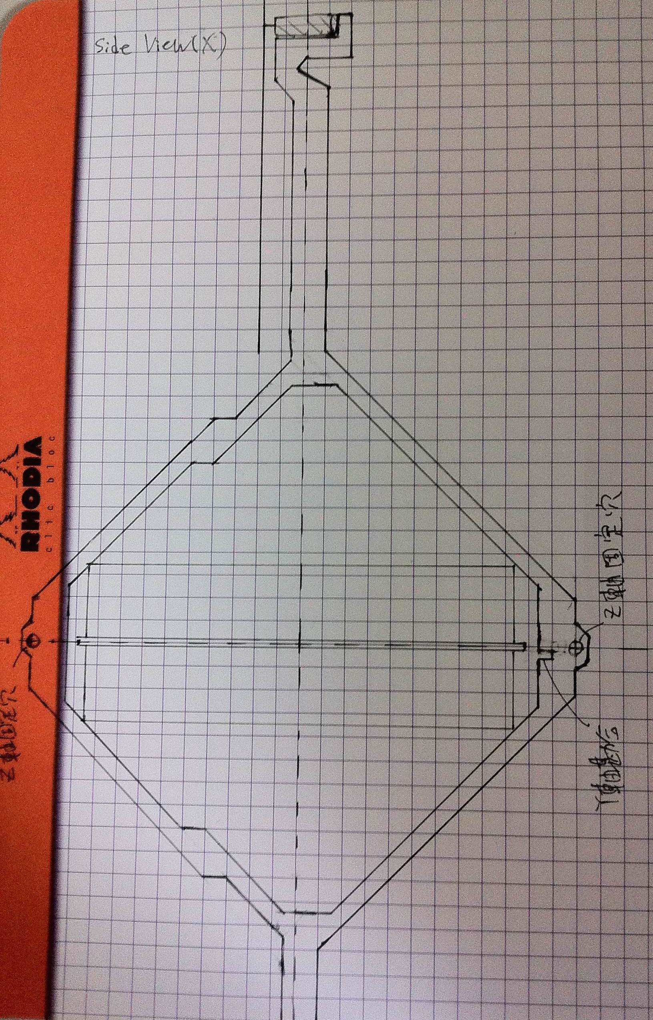
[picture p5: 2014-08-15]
devlog/picture/2014.08.11_side-view_X.JPG

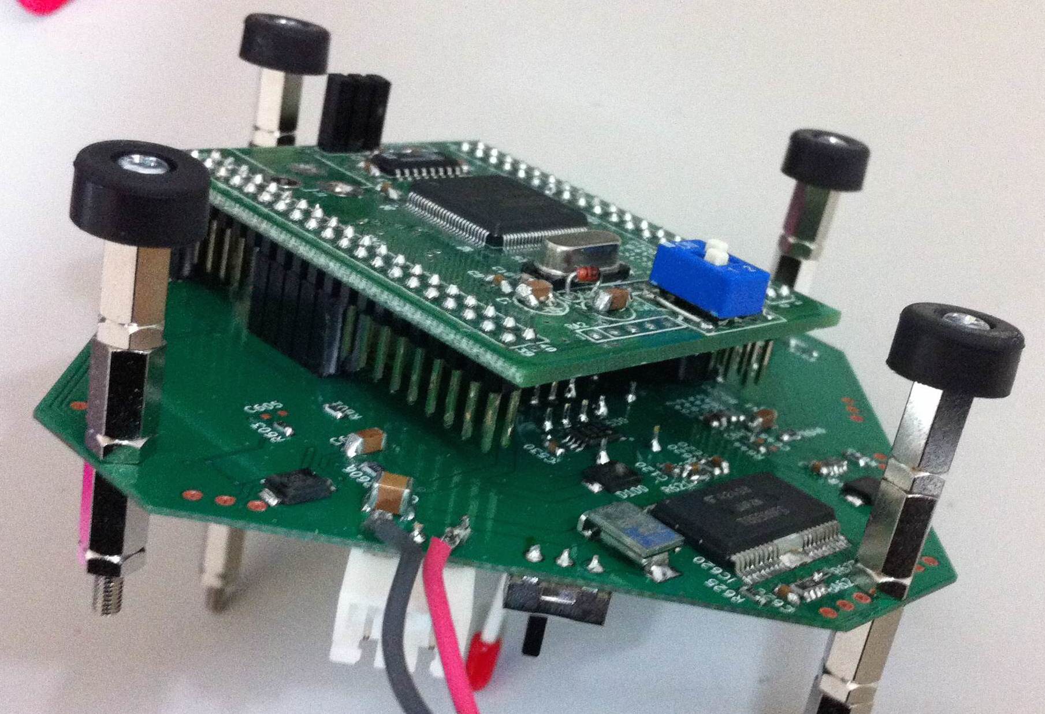
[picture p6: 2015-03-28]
devlog/picture/2015.03.25_2xBoard_B1.JPG

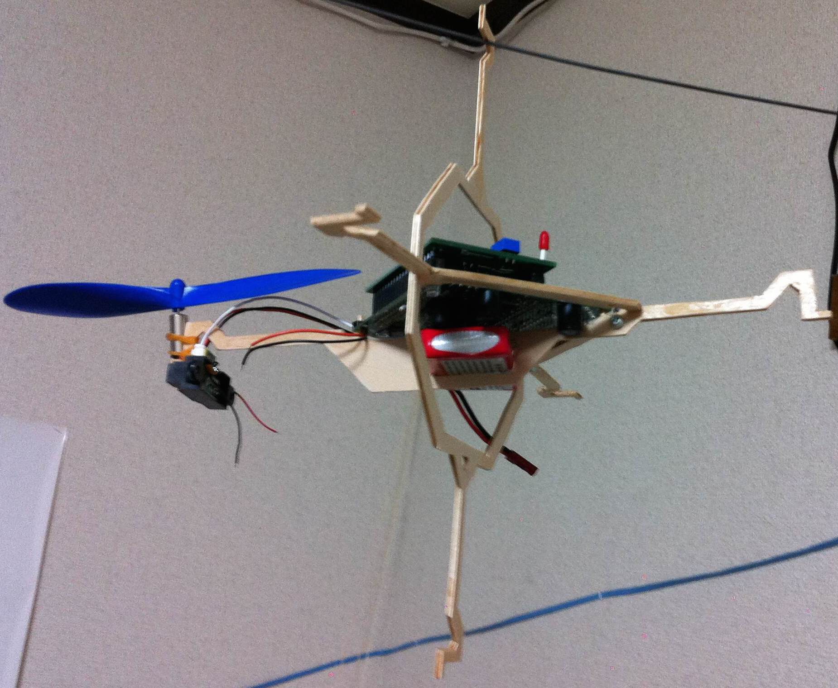
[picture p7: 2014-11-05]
devlog/picture/2014.11.04_frame_assy1.jpg

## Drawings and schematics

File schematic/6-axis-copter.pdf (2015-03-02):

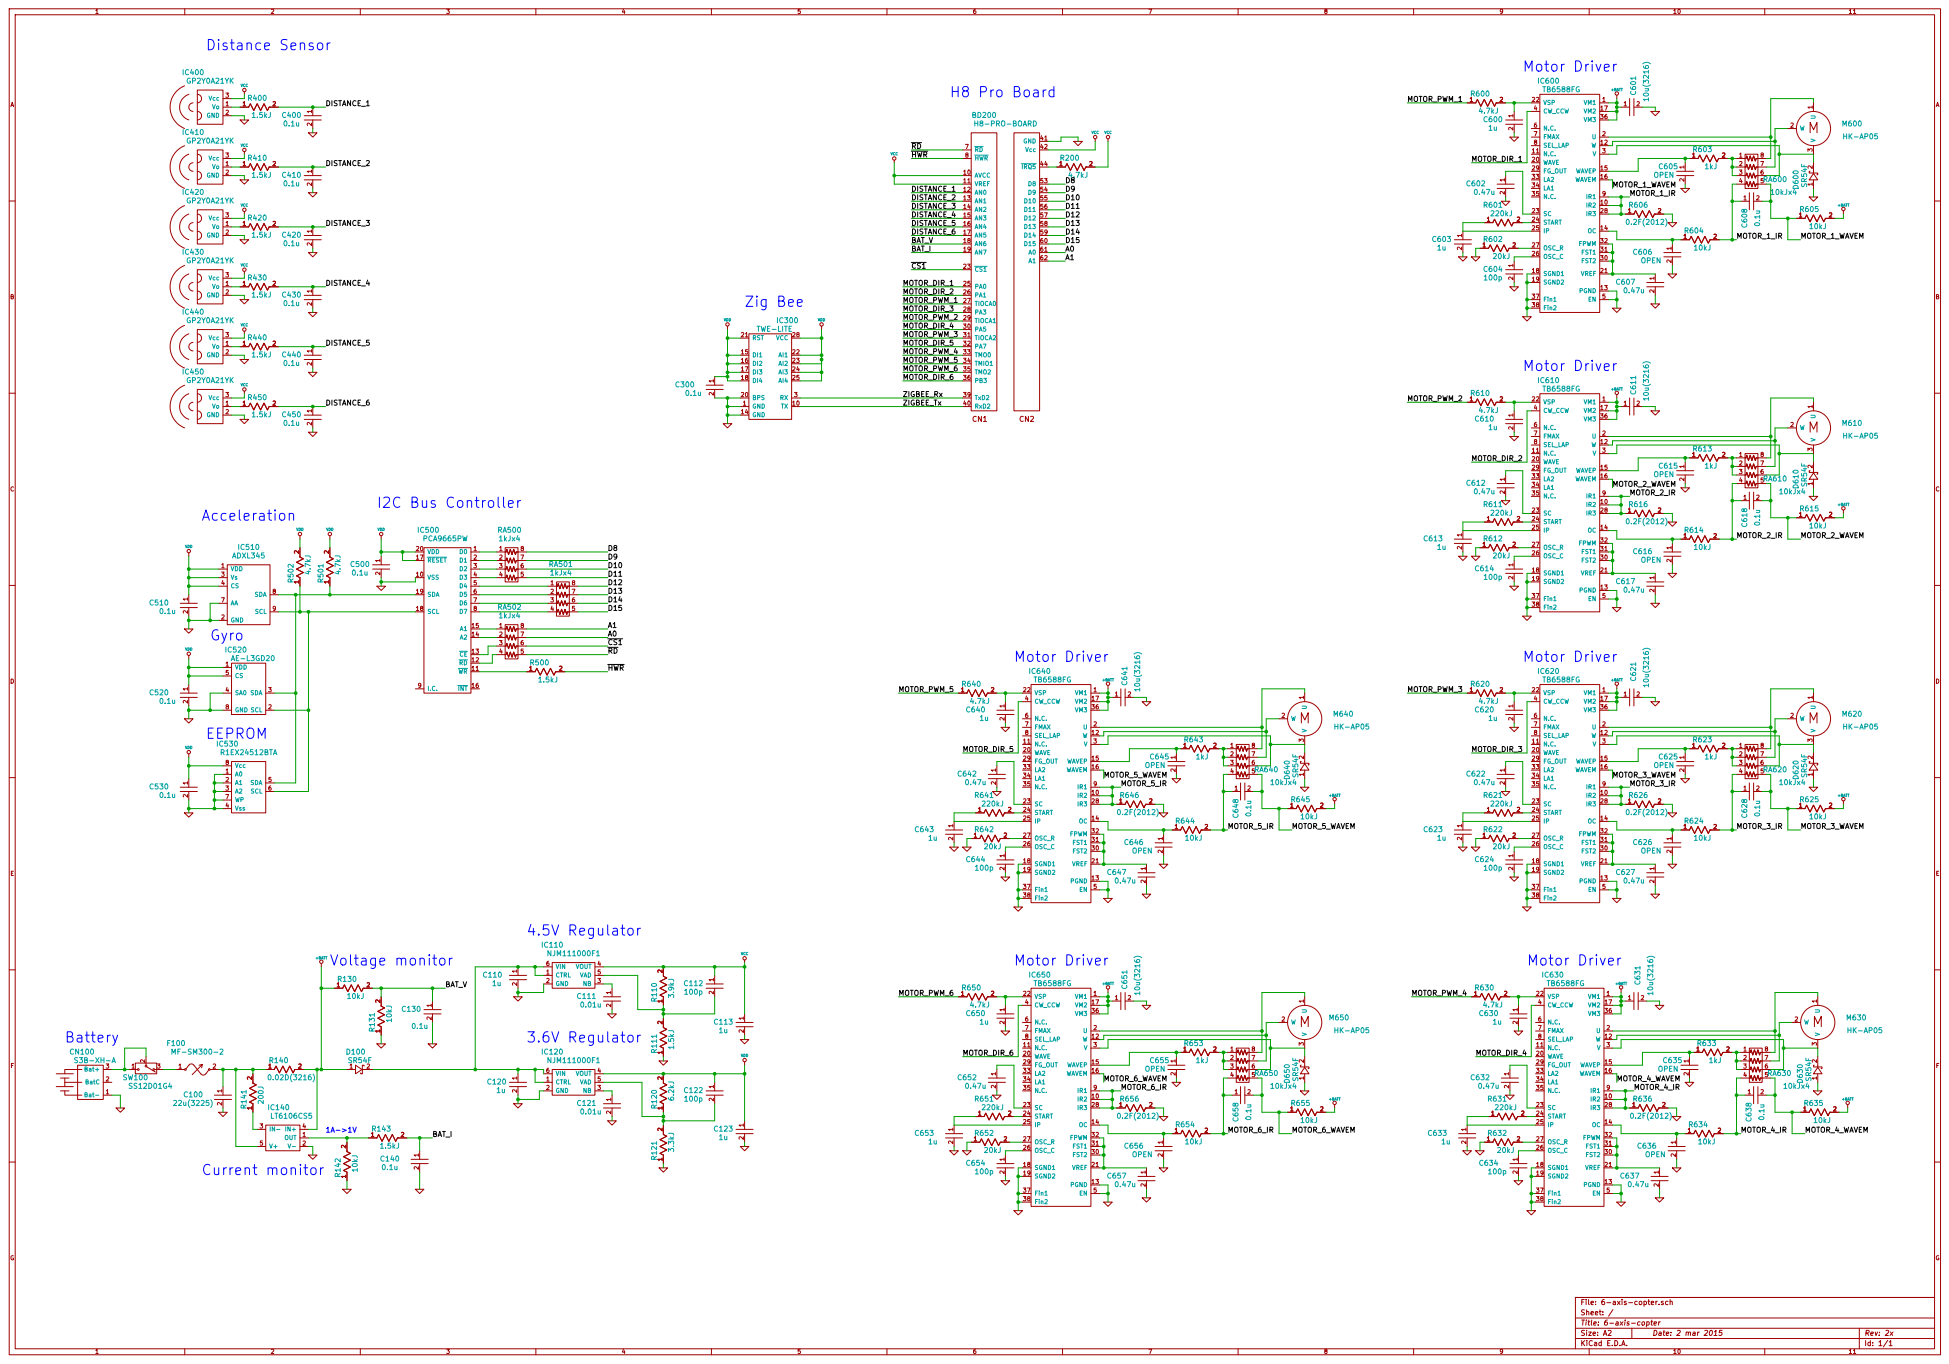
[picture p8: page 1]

File: 6-axis-copter.sch

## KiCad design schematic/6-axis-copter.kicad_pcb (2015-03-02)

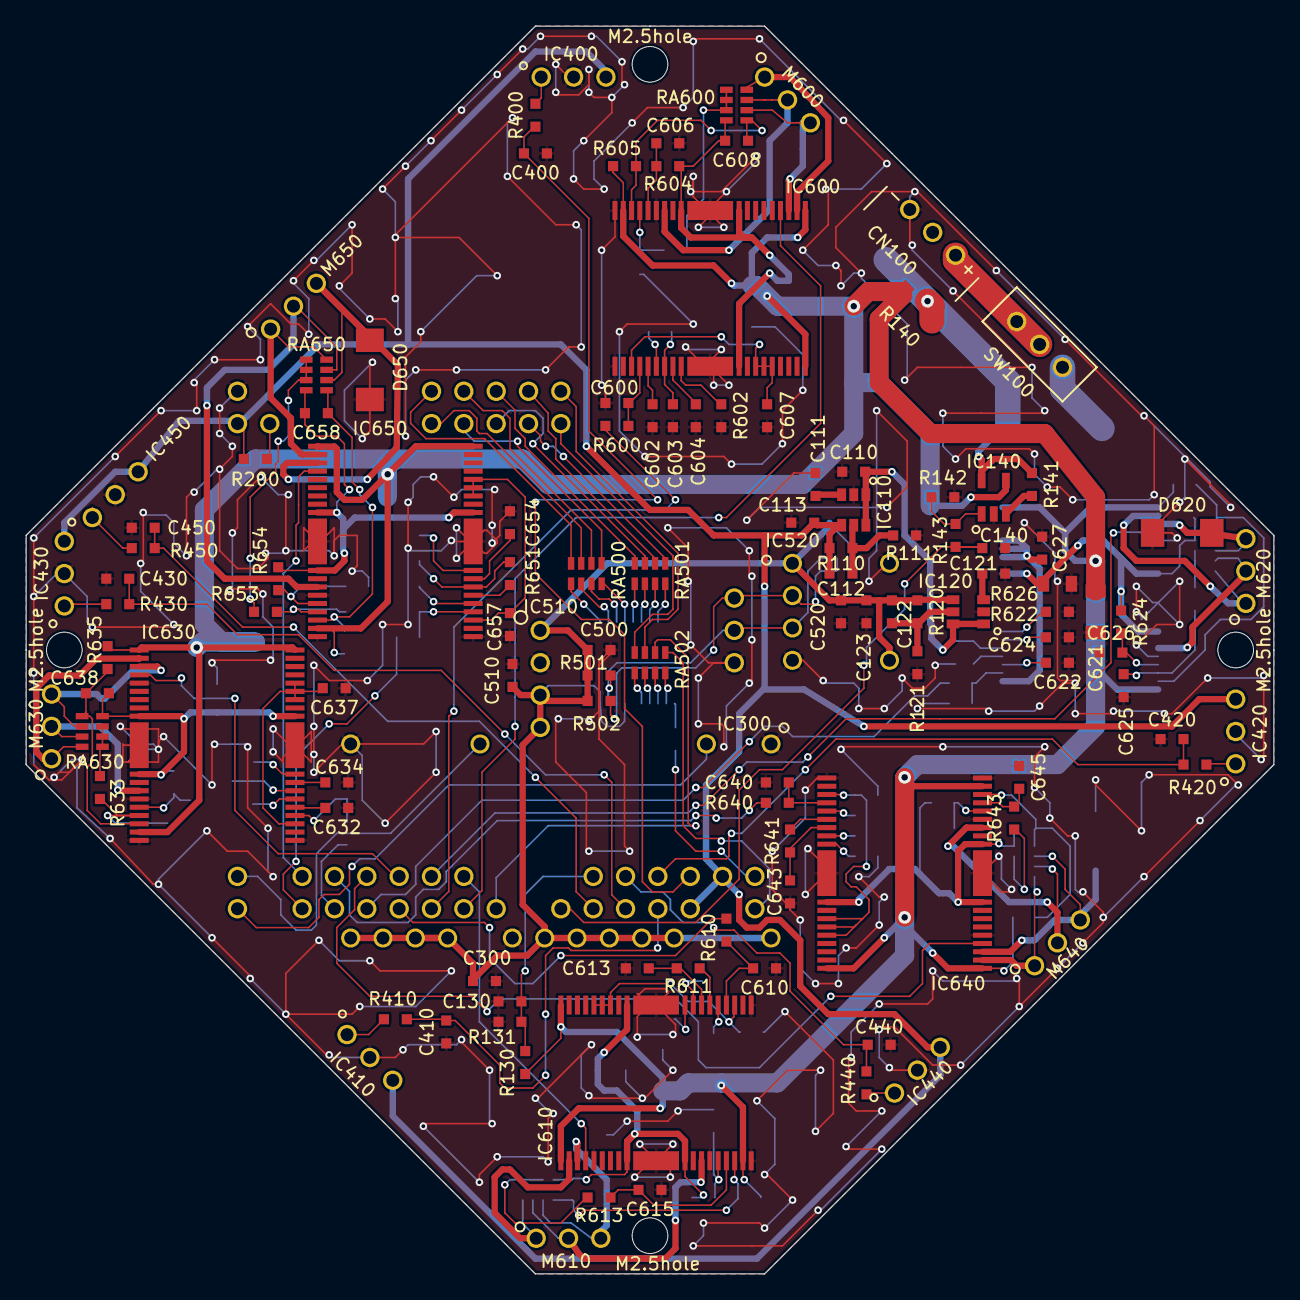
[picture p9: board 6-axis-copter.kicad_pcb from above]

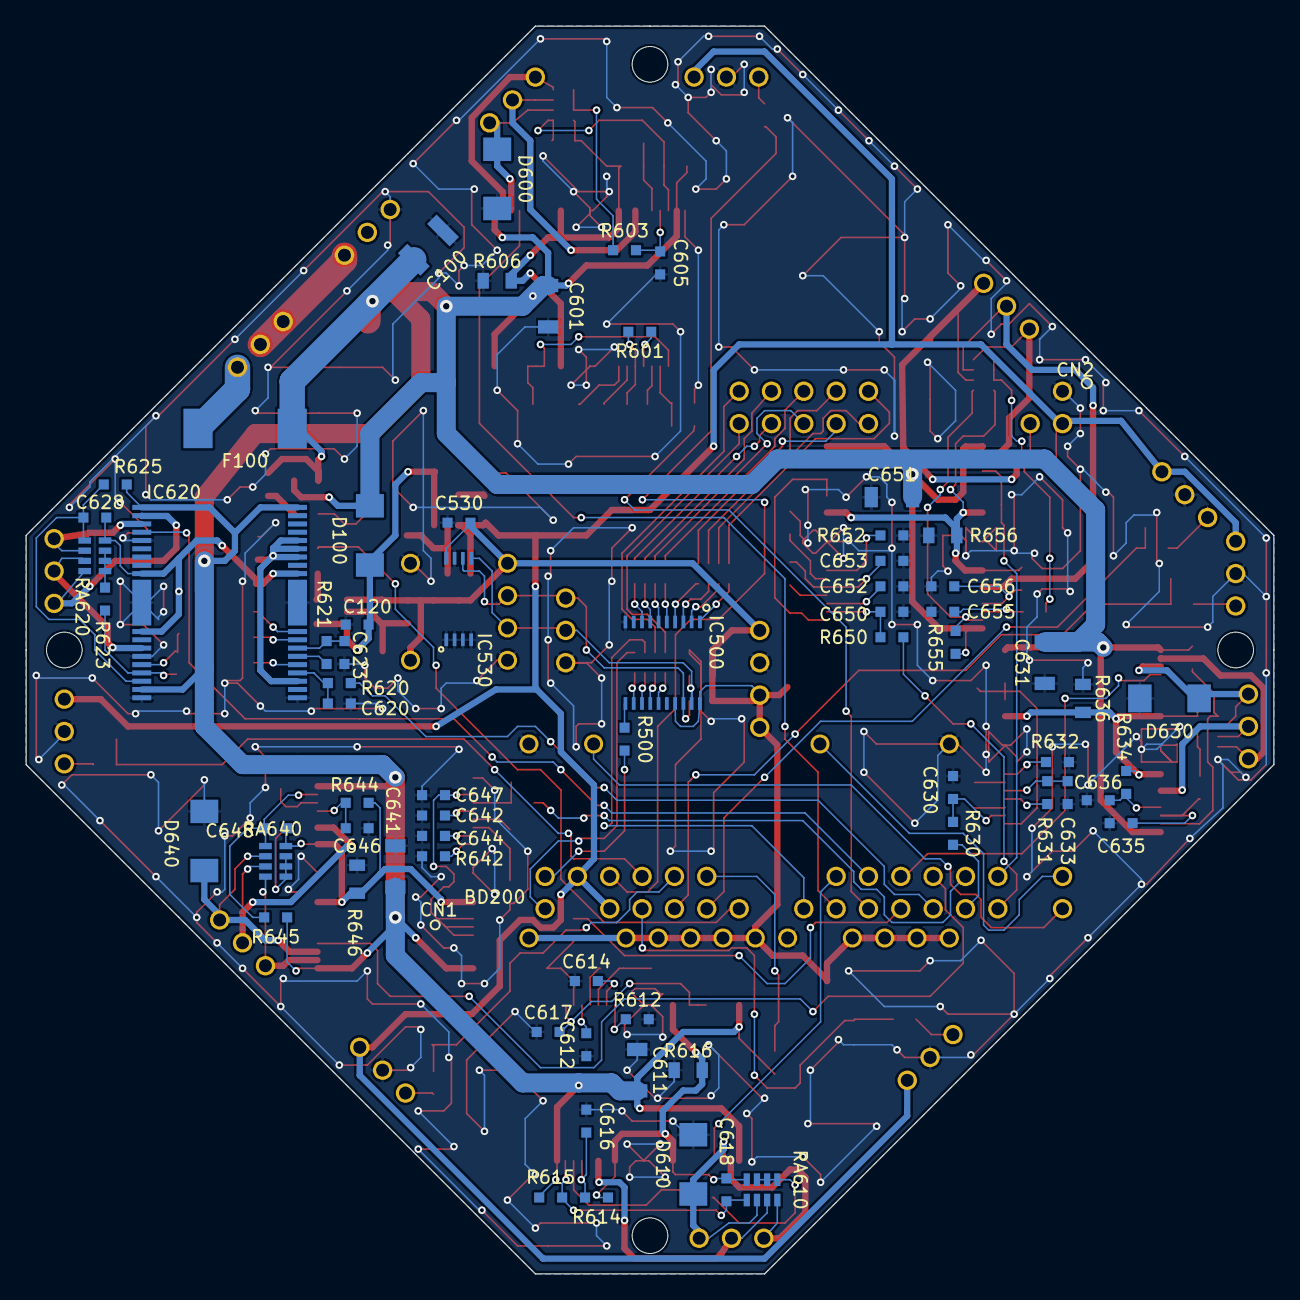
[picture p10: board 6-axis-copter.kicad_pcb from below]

Board: 2 copper layers, 98.0 x 98.0 mm, 188 parts (69 on the bottom side), 161 nets.

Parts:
BD200: H8-PRO
C100: 3225
C110, C111, C112, C113, C120, C121, C122, C123, C130, C140, C300, C400, C410, C420, C430, C440, C450, C500, C510, C520, C530, C600, C602, C603, C604, C605, C606, C607, C608, C610, C612, C613, C614, C615, C616, C617, C618, C620, C622, C623, C624, C625, C626, C627, C628, C630, C632, C633, C634, C635, C636, C637, C638, C640, C642, C643, C644, C645, C646, C647, C648, C650, C652, C653, C654, C655, C656, C657, C658: 1608
C601, C611, C621, C631, C641, C651: 3216
CN100: S3B-XH-A
D100, D600, D610, D620, D630, D640, D650: SR54F
F100: MF-SM300
IC110, IC120: SOT23-6
IC140: TSOP23-5
IC300: TWE-LITE
IC400, IC410, IC420, IC430, IC440, IC450: GP2Y0A21YK
IC500: TSSOP20
IC510: ADXL345
IC520: AE-L3GD20
IC530: TSSOP8
IC600, IC610, IC620, IC630, IC640, IC650: TB6588FG
M2.5hole, M2.5hole#2, M2.5hole#3, M2.5hole#4: M2.5hole
M600, M610, M620, M630, M640, M650: HK-AP05
R110, R111, R120, R121, R130, R131, R141, R142, R143, R200, R400, R410, R420, R430, R440, R450, R500, R501, R502, R600, R601, R602, R603, R604, R605, R610, R611, R612, R613, R614, R615, R620, R621, R622, R623, R624, R625, R630, R631, R632, R633, R634, R635, R640, R641, R642, R643, R644, R645, R650, R651, R652, R653, R654, R655: 1608
R140: 3216
R606, R616, R626, R636, R646, R656: 2012
RA500, RA501, RA502, RA600, RA610, RA620, RA630, RA640, RA650: BCN164AB
SW100: SS12D01G4

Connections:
+BATT: C601.1, C611.1, C621.1, C631.1, C641.1, C651.1, D100.1, IC140.4, IC600.1, IC600.17, IC600.36, IC610.1, IC610.17, IC610.36, IC620.1, IC620.17, IC620.36, IC630.1, IC630.17, IC630.36, IC640.1, IC640.17, IC640.36, IC650.1, IC650.17, IC650.36, R130.1, R140.2, R605.2, R615.2, R625.2, R635.2, R645.2, R655.2
/A0: BD200.61, RA502.7
/A1: BD200.62, RA502.8
/BAT_I: BD200.19, C140.1, R143.2
/BAT_V: BD200.18, C130.1, R130.2, R131.2
/D8: BD200.53, RA500.8
/D9: BD200.54, RA500.7
/D10: BD200.55, RA500.6
/D11: BD200.56, RA500.5
/D12: BD200.57, RA501.8
/D13: BD200.58, RA501.7
/D14: BD200.59, RA501.6
/D15: BD200.60, RA501.5
/DISTANCE_1: BD200.12, C400.1, R400.2
/DISTANCE_2: BD200.13, C410.1, R410.2
/DISTANCE_3: BD200.14, C420.1, R420.2
/DISTANCE_4: BD200.15, C430.1, R430.2
/DISTANCE_5: BD200.16, C440.1, R440.2
/DISTANCE_6: BD200.17, C450.1, R450.2
/MOTOR_1_IR: C608.1, IC600.9, IC600.10, IC600.28, R604.2, R606.1, RA600.4
/MOTOR_1_WAVEM: C608.2, IC600.16, R605.1, RA600.5
/MOTOR_2_IR: C618.1, IC610.9, IC610.10, IC610.28, R614.2, R616.1, RA610.4
/MOTOR_2_WAVEM: C618.2, IC610.16, R615.1, RA610.5
/MOTOR_3_IR: C628.1, IC620.9, IC620.10, IC620.28, R624.2, R626.1, RA620.4
/MOTOR_3_WAVEM: C628.2, IC620.16, R625.1, RA620.5
/MOTOR_4_IR: C638.1, IC630.9, IC630.10, IC630.28, R634.2, R636.1, RA630.4
/MOTOR_4_WAVEM: C638.2, IC630.16, R635.1, RA630.5
/MOTOR_5_IR: C648.1, IC640.9, IC640.10, IC640.28, R644.2, R646.1, RA640.4
/MOTOR_5_WAVEM: C648.2, IC640.16, R645.1, RA640.5
/MOTOR_6_IR: C658.1, IC650.9, IC650.10, IC650.28, R654.2, R656.1, RA650.4
/MOTOR_6_WAVEM: C658.2, IC650.16, R655.1, RA650.5
/MOTOR_DIR_1: BD200.25, IC600.4
/MOTOR_DIR_2: BD200.26, IC610.4
/MOTOR_DIR_3: BD200.28, IC620.4
/MOTOR_DIR_4: BD200.30, IC630.4
/MOTOR_DIR_5: BD200.32, IC640.4
/MOTOR_DIR_6: BD200.36, IC650.4
/MOTOR_PWM_1: BD200.27, R600.1
/MOTOR_PWM_2: BD200.29, R610.1
/MOTOR_PWM_3: BD200.31, R620.1
/MOTOR_PWM_4: BD200.33, R630.1
/MOTOR_PWM_5: BD200.34, R640.1
/MOTOR_PWM_6: BD200.35, R650.1
/ZIGBEE_Rx: BD200.39, IC300.3
/ZIGBEE_Tx: BD200.40, IC300.10
/~CS1: BD200.23, RA502.6
/~HWR: BD200.8, R500.2
/~RD: BD200.7, RA502.5
GND: BD200.41, C100.2, C110.2, C111.2, C113.2, C120.2, C121.2, C123.2, C130.2, C140.2, C300.2, C400.2, C410.2, C420.2, C430.2, C440.2, C450.2, C500.2, C510.2, C520.2, C530.2, C600.2, C601.2, C602.2, C603.2, C604.2, C605.2, C606.2, C607.2, C610.2, C611.2, C612.2, C613.2, C614.2, C615.2, C616.2, C617.2, C620.2, C621.2, C622.2, C623.2, C624.2, C625.2, C626.2, C627.2, C630.2, C631.2, C632.2, C633.2, C634.2, C635.2, C636.2, C637.2, C640.2, C641.2, C642.2, C643.2, C644.2, C645.2, C646.2, C647.2, C650.2, C651.2, C652.2, C653.2, C654.2, C655.2, C656.2, C657.2, CN100.1, D600.1, D610.1, D620.1, D630.1, D640.1, D650.1, IC110.2, IC120.2, IC140.2, IC300.1, IC300.14, IC300.20, IC400.2, IC410.2, IC420.2, IC430.2, IC440.2, IC450.2, IC500.10, IC510.2, IC510.7, IC520.4, IC520.8, IC530.1, IC530.2, IC530.3, IC530.4, IC530.7, IC600.5, IC600.13, IC600.18, IC600.19, IC600.37, IC600.38, IC610.5, IC610.13, IC610.18, IC610.19, IC610.37, IC610.38, IC620.5, IC620.13, IC620.18, IC620.19, IC620.37, IC620.38, IC630.5, IC630.13, IC630.18, IC630.19, IC630.37, IC630.38, IC640.5, IC640.13, IC640.18, IC640.19, IC640.37, IC640.38, IC650.5, IC650.13, IC650.18, IC650.19, IC650.37, IC650.38, R111.1, R121.1, R131.1, R142.1, R602.1, R606.2, R612.1, R616.2, R622.1, R626.2, R632.1, R636.2, R642.1, R646.2, R652.1, R656.2
unnamed: IC140.3, R141.1
unnamed: D630.2, IC630.3, M630.3, RA630.6
unnamed: C622.1, IC620.23
unnamed: C624.1, IC620.26
unnamed: C636.1, IC630.14, R634.1
unnamed: IC610.2, M610.1, RA610.8
unnamed: C617.1, IC610.21, IC610.30, IC610.31, IC610.32
unnamed: C604.1, IC600.26
unnamed: C612.1, IC610.23
unnamed: IC620.2, M620.1, RA620.8
unnamed: C627.1, IC620.21, IC620.30, IC620.31, IC620.32
unnamed: C614.1, IC610.26
unnamed: IC610.27, R612.2
unnamed: C637.1, IC630.21, IC630.30, IC630.31, IC630.32
unnamed: C635.1, IC630.15, R633.1
unnamed: IC630.27, R632.2
unnamed: IC630.24, R631.2
unnamed: C630.1, IC630.22, R630.2
unnamed: C633.1, IC630.25, R631.1
unnamed: C634.1, IC630.26
unnamed: C632.1, IC630.23
unnamed: C620.1, IC620.22, R620.2
unnamed: C623.1, IC620.25, R621.1
unnamed: IC620.24, R621.2
unnamed: C626.1, IC620.14, R624.1
unnamed: C625.1, IC620.15, R623.1
unnamed: IC620.27, R622.2
unnamed: D610.2, IC610.3, M610.3, RA610.6
unnamed: D620.2, IC620.3, M620.3, RA620.6
unnamed: R623.2, RA620.1, RA620.2, RA620.3
unnamed: C607.1, IC600.21, IC600.30, IC600.31, IC600.32
unnamed: C602.1, IC600.23
unnamed: IC600.2, M600.1, RA600.8
unnamed: IC620.12, M620.2, RA620.7
unnamed: IC650.27, R652.2
unnamed: C650.1, IC650.22, R650.2
unnamed: C653.1, IC650.25, R651.1
unnamed: IC650.24, R651.2
unnamed: C654.1, IC650.26
unnamed: C655.1, IC650.15, R653.1
unnamed: C652.1, IC650.23
unnamed: C644.1, IC640.26
unnamed: C647.1, IC640.21, IC640.30, IC640.31, IC640.32
unnamed: C642.1, IC640.23
unnamed: C656.1, IC650.14, R654.1
unnamed: IC650.2, M650.1, RA650.8
unnamed: R653.2, RA650.1, RA650.2, RA650.3
unnamed: C657.1, IC650.21, IC650.30, IC650.31, IC650.32
unnamed: D650.2, IC650.3, M650.3, RA650.6
unnamed: IC650.12, M650.2, RA650.7
unnamed: C646.1, IC640.14, R644.1
unnamed: IC640.27, R642.2
unnamed: C640.1, IC640.22, R640.2
unnamed: IC640.24, R641.2
unnamed: C643.1, IC640.25, R641.1
unnamed: R633.2, RA630.1, RA630.2, RA630.3
unnamed: IC630.12, M630.2, RA630.7
unnamed: IC630.2, M630.1, RA630.8
unnamed: D640.2, IC640.3, M640.3, RA640.6
unnamed: R643.2, RA640.1, RA640.2, RA640.3
unnamed: C645.1, IC640.15, R643.1
unnamed: IC640.12, M640.2, RA640.7
unnamed: IC640.2, M640.1, RA640.8
unnamed: IC500.12, RA502.4
unnamed: IC500.15, RA502.1
unnamed: BD200.44, R200.1
unnamed: C121.1, IC120.3
unnamed: CN100.3, SW100.1, SW100.2
unnamed: IC400.1, R400.1
unnamed: C122.2, IC120.5, R120.1, R121.2
unnamed: IC430.1, R430.1
unnamed: IC440.1, R440.1
unnamed: IC410.1, R410.1
unnamed: IC420.1, R420.1
unnamed: IC140.1, R142.2, R143.1
unnamed: F100.1, SW100.3
unnamed: C111.1, IC110.3
unnamed: C112.2, IC110.5, R110.1, R111.2
unnamed: IC500.14, RA502.2
unnamed: C100.1, F100.2, IC140.5, R140.1, R141.2
unnamed: C110.1, C120.1, D100.2, IC110.1, IC110.6, IC120.1, IC120.6
unnamed: IC500.18, IC510.9, IC520.2, IC530.6, R502.1
unnamed: IC500.19, IC510.8, IC520.3, IC530.5, R501.1
unnamed: IC500.6, RA501.2
unnamed: IC500.1, RA500.1
unnamed: IC500.2, RA500.2
unnamed: IC500.3, RA500.3
unnamed: IC500.4, RA500.4
unnamed: IC500.5, RA501.1
unnamed: IC500.7, RA501.3
unnamed: IC500.8, RA501.4
unnamed: IC500.11, R500.1
unnamed: IC500.13, RA502.3
unnamed: IC450.1, R450.1
unnamed: R603.2, RA600.1, RA600.2, RA600.3
unnamed: R613.2, RA610.1, RA610.2, RA610.3
unnamed: C606.1, IC600.14, R604.1
unnamed: D600.2, IC600.3, M600.3, RA600.6
unnamed: C605.1, IC600.15, R603.1
unnamed: IC600.12, M600.2, RA600.7
unnamed: C616.1, IC610.14, R614.1
unnamed: C613.1, IC610.25, R611.1
unnamed: IC610.12, M610.2, RA610.7
unnamed: C615.1, IC610.15, R613.1
unnamed: C610.1, IC610.22, R610.2
unnamed: IC610.24, R611.2
unnamed: C603.1, IC600.25, R601.1
unnamed: IC600.24, R601.2
unnamed: IC600.27, R602.2
unnamed: C600.1, IC600.22, R600.2
VCC: BD200.10, BD200.11, BD200.42, C112.1, C113.1, IC110.4, IC400.3, IC410.3, IC420.3, IC430.3, IC440.3, IC450.3, R110.2, R200.2
VDD: C122.1, C123.1, C300.1, C500.1, C510.1, C520.1, C530.1, IC120.4, IC300.15, IC300.16, IC300.17, IC300.18, IC300.21, IC300.22, IC300.23, IC300.24, IC300.25, IC300.28, IC500.17, IC500.20, IC510.1, IC510.3, IC510.4, IC520.1, IC520.5, IC530.8, R120.2, R501.2, R502.2

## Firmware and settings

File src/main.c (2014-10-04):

#include "defines.h"
#include "lib.h"
#include "pi.h"
#include "interrupt.h"

static int
init (void)
{
  extern int16 data_start_load, data_start, edata, bss_start, ebss;

  /* 割込を無効にする */
  INTR_DISABLE;

  /* PA=VA処理転送 */
  memory_data_copy (&data_start, &data_start_load,
                    (long) &edata - (long) &data_start);
  set_data_in_memory (&bss_start, 0, (long) &ebss - (long) &bss_start);

  serial_init ();
  DRAM_init ();
  internal_timer_init ();
  motor_driver_init ();
  ADC_init ();
  I2C_init ();

  put_string ("boot succeed\n");
  
  /* 割込を有効にする */
  INTR_ENABLE;

  return 0;
}

static void
test (void)
{
  /* DRAMテスト */
  extern int16 dram_start;
  static int8 *dram_addr = (int8 *) (&dram_start);

  put_string (" DRAM test\n");
  *dram_addr = 0x55;
  if(*dram_addr != 0x55)
    {
      put_string ("  err\n");
    }
  else
    {
      put_string ("  ok\n");
    }
}

int
main (void)
{
  init ();
  test ();

  while (1)
    {
      asm volatile ("sleep");
    }

  return 0;
}

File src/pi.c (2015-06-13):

#include "defines.h"
#include "pi.h"

#include "p_serial.h"
#include "p_dram.h"
#include "p_port.h"
#include "p_timer.h"
#include "p_ADC.h"
#include "p_I2C.h"

////////////////////serial interface////////////////////
static void
debug_serial_init (void)
{
  disable_SCI1_TxRx ();
  disable_SCI1_serial_interrupt ();

  set_SCI1_clock_source_and_SCK_port_status ();
  set_SCI1_serial_modes ();
  set_SCI1_bitrate ();

  /* enable_SCI1_serial_interrept (); */
  enable_SCI1_TxRx ();
}

static void
zigbee_serial_init (void)
{
  disable_SCI2_TxRx ();
  disable_SCI2_serial_interrupt ();

  set_SCI2_clock_source_and_SCK_port_status ();
  set_SCI2_serial_modes ();
  set_SCI2_bitrate ();

  enable_SCI2_serial_interrupt ();
  enable_SCI2_TxRx ();
}

void
serial_init (void)
{
  debug_serial_init ();
  zigbee_serial_init ();
}

static void
put_char (uint8 c)
{
  if (c == '\n')
    serial_send_byte ('\r');
  serial_send_byte (c);
}

void
put_byte_data (uint8 c)
{
  serial_send_byte (c);
}

uint8
get_char (void)
{
  uint8 c = serial_recv_byte ();
  c = (c == '\r') ? '\n' : c;

  return c;
}

uint8
get_byte_data (void)
{
  uint8 c = serial_recv_byte ();
  return c;
}

void
put_string (int8 str[])
{
  while (*str)
    put_char (*(str++));
}

/* TODO：バッファサイズのチェックを追加 */
/* if((int)sizeof(command) < get_string(command)) */
/*   put_string("command too long\n"); */
int16
get_string (int8 *store_array)
{
  int16 i = 0;
  uint8 c;

  do
    {
      c = get_char ();
      if (c == '\n')
        c = '\0';
      store_array[i++] = c;
    }
  while (c);
  return i - 1;
}

void
put_hex (uint32 value, int16 digit_number)
{
  int8 hex_buffer[9];
  int8 *hex_pointer;

  hex_pointer = hex_buffer + sizeof(hex_buffer) - 1;
  *(hex_pointer--) = '\0';
  while (digit_number)
    {
      *(hex_pointer--) = "0123456789ABCDEF"[value & 0xf];
      value >>= 4;
      digit_number--;
    }
  put_string (hex_pointer + 1);
}

void
put_dec (uint16 value)
{
  int8 dec_buffer[9];
  int8 *dec_pointer;
  int16 value_size = sizeof(value);

  dec_pointer = dec_buffer + sizeof(dec_buffer) - 1;
  *(dec_pointer--) = '\0';
  while (value)
    {
      *(dec_pointer--) = "0123456789"[value % 10];
      value /= 10;
      value_size--;
    }
  put_string (dec_pointer + 1);
}

////////////////////timer interface////////////////////
static void
timer8_0ch_pwm_init (void)
{
  disable_TMR8ch0_interrupt ();
  set_TMO0_pin_function ();
  set_TMR8ch0_counter_reset_condition ();
  set_TMR8ch0_compare_match_register ((uint8) 40);
  set_TMR8ch0_clock_source ();
}

static void
timer8_1ch_pwm_init (void)
{
  disable_TMR8ch1_interrupt ();
  set_TMIO1_pin_function ();
  set_TMR8ch1_counter_reset_condition ();
  set_TMR8ch1_compare_match_register ((uint8) 40);
  set_TMR8ch1_clock_source ();
}

static void
timer8_2ch_pwm_init (void)
{
  disable_TMR8ch2_interrupt ();
  set_TMO2_pin_function ();
  set_TMR8ch2_counter_reset_condition ();
  set_TMR8ch2_compare_match_register ((uint8) 40);
  set_TMR8ch2_clock_source ();
}

static void
timer8_3ch_init (void)
{
  disable_TMR8ch3_interrupt ();
  set_TMIO3_pin_function ();
  select_TMR8ch3_function ();
  set_TMR8ch3_counter_reset_condition ();
  set_TMR8ch3A_compare_match_register ();
  enable_TMR8ch3A_interrept ();
  set_TMR8ch3_clock_source ();
}

static void
timer16_0ch_pwm_init (void)
{
  disable_TMR16ch0 ();
  disable_TMR16ch0A_interrupt ();

  set_TMR16ch0_clock_source ();
  set_TMR16ch0_counter_reset_condition ();
  set_TMR16ch0_compare_match_register ((uint8) 40);
  set_TIOCA0_pin_function ();

  enable_TMR16ch0 ();
}

static void
timer16_1ch_pwm_init (void)
{
  disable_TMR16ch1 ();
  disable_TMR16ch1A_interrupt ();

  set_TMR16ch1_clock_source ();
  set_TMR16ch1_counter_reset_condition ();
  set_TMR16ch1_compare_match_register ((uint8) 40);
  set_TIOCA1_pin_function ();

  enable_TMR16ch1 ();
}

static void
timer16_2ch_pwm_init (void)
{
  disable_TMR16ch2 ();
  disable_TMR16ch2A_interrupt ();

  set_TMR16ch2_clock_source ();
  set_TMR16ch2_counter_reset_condition ();
  set_TMR16ch2_compare_match_register ((uint8) 40);
  set_TIOCA2_pin_function ();

  enable_TMR16ch2 ();
}

void
internal_timer_init (void)
{
  timer8_3ch_init ();
}

void
clear_TMR8ch3A_compare_match_flag ()
{
  clear_TMR8ch3_CMFA ();
}

////////////////////motor driver interface////////////////////
void
motor_driver_init (void)
{
  timer8_0ch_pwm_init ();
  timer8_1ch_pwm_init ();
  timer8_2ch_pwm_init ();
  timer16_0ch_pwm_init ();
  timer16_1ch_pwm_init ();
  timer16_2ch_pwm_init ();

  motor_driver_direction_enable ();
  motor_driver1_direction ((bool)1);
  motor_driver2_direction ((bool)1);
  motor_driver3_direction ((bool)1);
  motor_driver4_direction ((bool)1);
  motor_driver5_direction ((bool)1);
  motor_driver6_direction ((bool)1);
}

/* TODO:99以上-99以下はリターン */
/* TODO:40の下は-40，-40の上は40になるように(-40〜40はペラが回らない)*/
void
set_Yp_PWM (int8 duty)
{
  if (duty < 0)
  {
    motor_driver1_direction ((bool)0);
    duty *= -1;
    set_TMR16ch0_compare_match_register ((uint8)duty);
  }
  else
  {
    motor_driver1_direction ((bool)1);
    set_TMR16ch0_compare_match_register ((uint8)duty);
  }
}

void
set_Yn_PWM (int8 duty)
{
  if (duty < 0)
  {
    motor_driver2_direction ((bool)0);
    duty *= -1;
    set_TMR16ch1_compare_match_register ((uint8)duty);
  }
  else
  {
    motor_driver2_direction ((bool)1);
    set_TMR16ch1_compare_match_register ((uint8)duty);
  }
}

void
set_Xp_PWM (int8 duty)
{
  if (duty < 0)
  {
    motor_driver3_direction ((bool)0);
    duty *= -1;
    set_TMR16ch2_compare_match_register ((uint8)duty);
  }
  else
  {
    motor_driver3_direction ((bool)1);
    set_TMR16ch2_compare_match_register ((uint8)duty);
  }
}

void
set_Xn_PWM (int8 duty)
{
  if (duty < 0)
  {
    motor_driver4_direction ((bool)0);
    duty *= -1;
    set_TMR8ch0_compare_match_register ((uint8)duty);
  }
  else
  {
    motor_driver4_direction ((bool)1);
    set_TMR8ch0_compare_match_register ((uint8)duty);
  }
}

void
set_Zp_PWM (int8 duty)
{
  if (duty < 0)
  {
    motor_driver5_direction ((bool)0);
    duty *= -1;
    set_TMR8ch1_compare_match_register ((uint8) duty);
  }
  else
  {
    motor_driver5_direction ((bool)1);
    set_TMR8ch1_compare_match_register ((uint8) duty);
  }
}

void
set_Zn_PWM (int8 duty)
{
  if (duty < 0)
  {
    motor_driver6_direction ((bool)0);
    duty *= -1;
    set_TMR8ch2_compare_match_register ((uint8) duty);
  }
  else
  {
    motor_driver6_direction ((bool)1);
    set_TMR8ch2_compare_match_register ((uint8) duty);
  }
}

int8
get_Yp_PWM (void)
{
  int8 duty;
  bool dir;

  duty = get_TMR16ch0_compare_match_register ();
  dir = get_motor_driver1_direction ();
  if(dir == 0)
    duty *= -1;

  return duty;
}

int8
get_Yn_PWM (void)
{
  int8 duty;
  bool dir;

  duty = get_TMR16ch1_compare_match_register ();
  dir = get_motor_driver2_direction ();
  if(dir == 0)
    duty *= -1;

  return duty;
}
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

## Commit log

2014-08-23 書き込みテスト serialでhello worldを返すプログラム．水晶発振子25MHzでの書き込みテスト
2014-08-24 前プロジェクトを元にリファクタリング,VA=PA転送実装
2014-08-24 DRAM実装
2014-08-24 timer/timer割り込み実装
2014-08-24 周辺情報更新
    [hardware.ods]
2014-08-30 TIOCA0にPWM出力を実装
2014-08-30 TIOCA1にPWM出力を実装
2014-08-30 TIOCA2にPWM出力を実装
2014-08-30 TMO0にPWM出力を実装
2014-08-30 TMIO1にPWM出力を実装
2014-08-30 TMO2にPWM出力を実装
2014-08-31 makeでTAGSファイルを生成するようMakefileを修正
2014-08-31 IRQ5にプルアップ抵抗追加(オープンドレイン)
    [6-axis-copter.sch]
2014-09-06 回路図の不要な配線を削除
    [6-axis-copter.sch]
2014-09-07 AN0のAD値取得を実装
2014-09-08 AN1のAD値取得を実装
2014-09-08 リファクタリング(ADチャネルセレクトを汎用関数に切り出し)
2014-09-08 AN2~7のAD値取得を実装
2014-09-08 timer_init()からモータドライバの初期化を切り出してenable出力を追加
2014-09-15 I2Cバスコントローラ/加速度センサのデバイス情報追加
    [hardware.ods]
2014-09-15 TAGSファイルを生成する際に削除してから生成するように変更
2014-09-17 SCI2にzigbeeシリアル送信実装
2014-09-18 zigbeeからのコマンド受信割り込み実装
2014-09-20 SCI0をSCI1という記述に修正 SCI1に対し勘違いしてSCI0という名前をつけていたため
2014-10-04 I2Cバスコン及び加速度センサからのデータ読み出しを実装
    [hardware.ods]
2014-10-05 角速度センサからのデータ読み出しを実装
2014-10-05 リファクタリング(I2Cからの連続2バイト読みだし関数の変数名を汎用化)
2014-10-05 周辺情報の進捗更新
2014-10-05 角速度センサの読み出しを2バイト読み出しに変更
    [hardware.ods]
2014-10-05 モニタツール first commit(コンソールにD1の値のみを表示)
2014-10-05 モニタツールにD1を出力する簡易グラフ実装
2014-10-06 モニタツールで16進加速度データを物理値にして出力できるよう変更
2014-10-06 リファクタリング(データ格納関数を分離)
2014-10-06 モニタツールに全ての受信データ取り込みを実装
2014-10-08 モニタツールのAXにゼロ点補正と速度・距離計算を仮実装
2014-10-09 モニタツールの速度計算をブールの公式で再実装
2014-10-09 モニタツールに角度算出を実装(ブールの公式)
2014-10-11 回路図の配線ミスを修正
    [6-axis-copter.sch]
2014-10-11 回路図のバッテリーシンボル・フットプリント修正
    [6-axis-copter.sch]
2014-10-11 回路図のH8ボードフットプリントを修正
2014-10-11 回路図のモーターに直列にコイル追加
    [6-axis-copter.sch]
2014-10-11 回路図：DIP部品のサイズ修正
2014-10-11 回路図にバッテリーSW追加
    [6-axis-copter.sch]
2014-10-14 PCBボード図作成
    [6-axis-copter.brd, 6-axis-copter.sch]
2014-10-15 基板製造メーカー(P板.com)の指摘を元にPCBボード図を修正
    [6-axis-copter.brd]
2014-10-18 部品表作成
    [bom.ods]
2014-10-18 readmeの進捗，ディレクトリ構成を更新
2014-10-26 周辺情報更新(筐体設計変更)
2014-10-31 周辺情報更新(筐体設計再変更)
2014-11-05 筐体仮作成
2014-11-08 筐体ASSY用スタンド作成
2014-11-13 モニタツールをQtで実装開始 シリアル入力をデバッグコンソールに出力
2014-11-14 モニタツール：シリアルのpublic変数・関数を極力privateに隠蔽
2014-11-15 dataクラス実装 serial_ifで受け取ったデータをdataクラスへ渡し格納
2014-11-16 モニタツール：シリアルデータの取りこぼしをなくすよう修正
2014-11-28 モニタツール：QMLでZ軸の加速度をグラフ表示 scene graphのサンプルコード"graph"をベースに作成
2014-11-29 浮力不足によりブラシレスモータに方針転換
2014-12-13 ブラシレスモータドライバデータシートまとめ
    [hardware.ods]
2015-01-10 モータ回転成功，浮力不足のためドライバ再選定が必要
    [hardware.ods]
2015-02-01 DRV11873で再挑戦．モータ回転せず，ドライバ再々選定が必要
2015-02-28 TB6588で再挑戦．ある程度浮力が出たため2x基板を作成(基板CADをkicadに変更)
    [6-axis-copter.brd, 6-axis-copter.kicad_pcb, 6-axis-copter.sch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]
2015-03-02 3Dプリンタ用筐体仮設計
2015-03-22 3Dプリンタ用筐体データ作成
    [bom.ods, flame.f3d, frame_for_2x.FCStd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]
2015-03-28 2x基板部品実装完了
2015-03-28 モニタツール：シリアルデータの取りこぼしを軽減
2015-03-29 10msで取得したセンサ値を80msで平均してシリアル出力する処理を実装
2015-04-04 モータdutyのgetter,setter実装
2015-04-04 UVLO実装
2015-04-29 バッテリ2S->3Sに変更しホバー仮実装．筐体破損のため再設計
    [frame_for_2x.FCStd, frame_for_2x.stl]
2015-05-01 モニタツール：グラフを増殖しパネル状に配置
2015-06-13 筐体衝突時のモータ停止(OverShockLockOut)実装
2015-06-13 4.5V低下・モーター脱調を軽減するためハード改造 負荷が大きすぎたため5Vレギュレータ変更． モータードライバのカレントリミットを積分&回転数変動時の応答速度を遅くしモーター脱調を軽減． 電圧低下を軽減するためリポバッテリの容量増加しモーター直列に抵抗追加． 軽量化のため基板のNC_DIP_pin抜き&筐体足切断し縫い糸で補強
2015-06-20 姿勢制御に使用するセンサ値を平均値から移動平均値に変更
2015-06-20 姿勢制御に角速度センサ値を追加し回転抑制する処理を追加
2015-06-20 加速度センサ初期値を実測値から決定
2015-06-20 モニタツール：データ受信がなければグラフの更新を停止するように変更
2015-06-21 モニタツール：コマンド送信ボタン実装
